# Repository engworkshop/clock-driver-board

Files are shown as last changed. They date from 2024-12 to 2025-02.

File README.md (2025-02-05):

# clock-driver-board
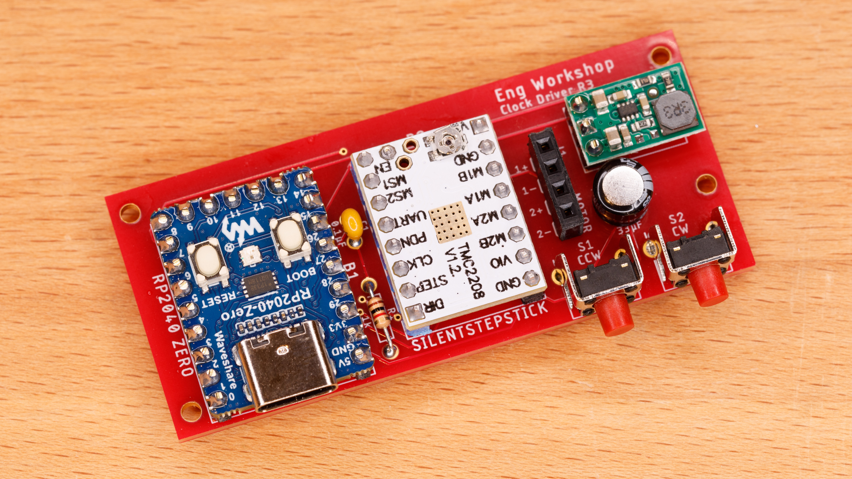
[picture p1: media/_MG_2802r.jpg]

This repository contains design files for an optional custom printed circuit board (PCB) for the [Mystery Clock](https://makerworld.com/en/models/764838) and [Hollow Clock 4 Remix](https://makerworld.com/en/models/875220) projects on [MakerWorld](https://makerworld.com/en/@EngWorkshop). This custom driver board incorporates 3 improvements. First, a dedicated real-time clock (RTC) chip, the Maxim DS3234, provides significantly greater timekeeping accuracy than the RP2040’s internal clock. The DS3234 incorporates temperature compensation to achieve its improved accuracy. Second, a dedicated stepper motor driver module provides quieter motor operation compared to the original design’s ULN2003 chip. The motor driver module incorporates the Trinamic TMC2208, which uses a “chopper drive” for quieter operation. Third, 2 pushbuttons allow fine adjustment of the hands.

The clock projects use a small, inexpensive 28BYJ-48 5V unipolar stepper motor. This motor must be converted to a bipolar configuration before it can be used with the clock driver board’s TMC2208 chip, which is designed for bipolar stepper motors. Motor conversion instructions are included at the bottom of this README file.

(All products shown or mentioned are items that I actually use and have found to work well. I have no relationship with any product supplier.)

## 1.&nbsp;&nbsp; The Circuit
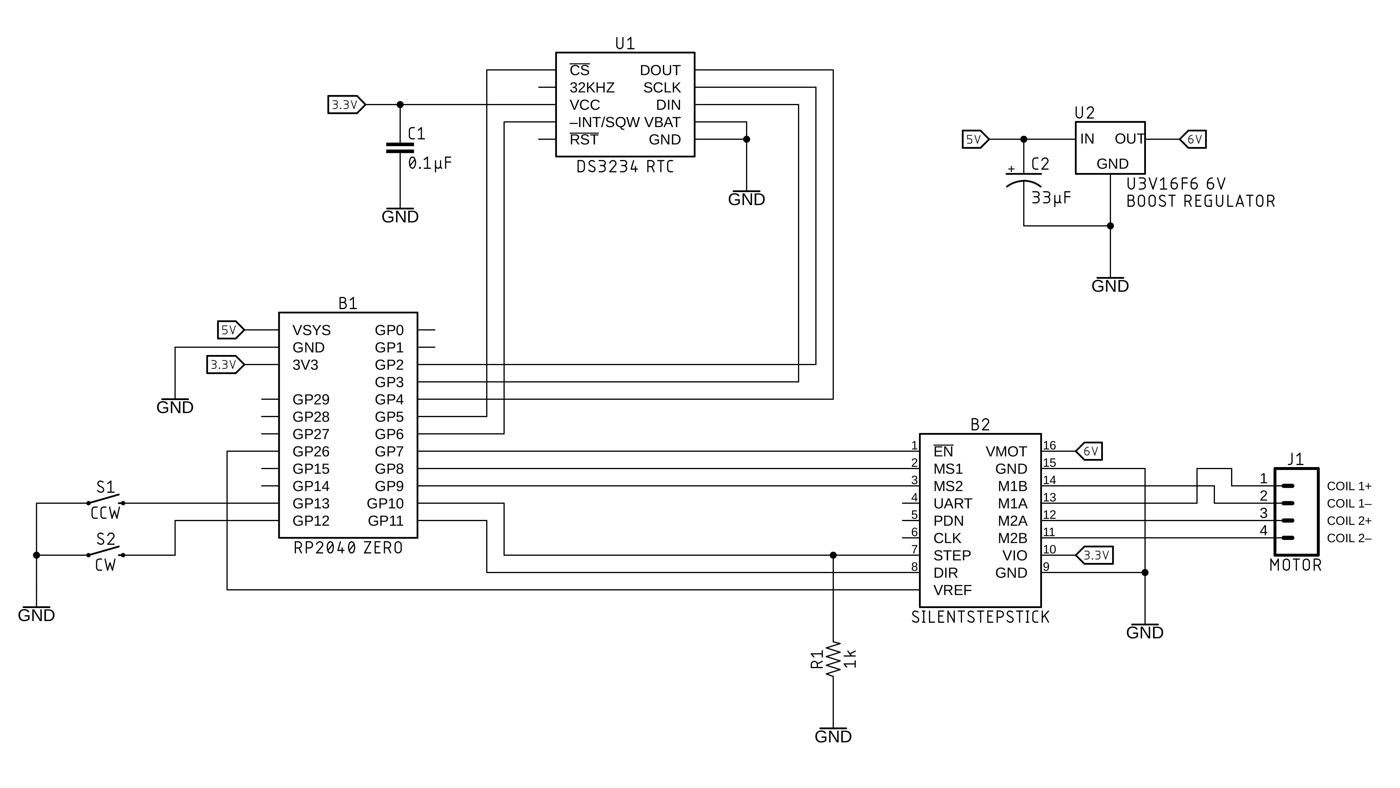
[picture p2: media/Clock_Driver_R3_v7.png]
schematic


**Circuit Description**

The RP2040 microcontroller communicates with the DS3234 RTC using the SPI bus. The clock chip is configured in software to send an interrupt to the microcontroller once every minute. In response to the interrupt, the microcontroller moves the minute hand through the TMC2208 motor driver. A pull-down resistor on the motor driver’s STEP input prevents spurious motor stepping during startup. A 6V boost regulator satisfies the motor driver module’s minimum supply voltage of 5.5V.

**Parts List**
- [Waveshare RP2040-Zero](https://www.waveshare.com/rp2040-zero.htm) microcontroller board without pin headers
- [TMC2208 SilentStepStick](https://www.amazon.com/gp/product/B08DFVZV5Q) stepper motor driver module
- [Pololu U3V16F6](https://www.pololu.com/product/4942) 6V boost voltage regulator
- Maxim DS3234 real-time clock chip ([DigiKey DS3234SN#-ND](https://www.digikey.com/en/products/detail/analog-devices-inc-maxim-integrated/DS3234SN/1197584))
- (2) C&K PTS645VK58-2LFS right angle tactile switches ([DigiKey CKN10965-ND](https://www.digikey.com/en/products/detail/c-k/PTS645VK58-2-LFS/3861398))
- 33 µF electrolytic capacitor (for example, [DigiKey P977-ND](https://www.digikey.com/en/products/detail/panasonic-electronic-components/ECE-A1EKS330/160557))
- 1 kΩ resistor (for example, [DigiKey 1.0KEBK-ND](https://www.digikey.com/en/products/detail/yageo/CFR-12JB-52-1K/4000))
- 0.1 µF ceramic capacitor (for example, [DigiKey 399-4264-ND](https://www.digikey.com/en/products/detail/kemet/C320C104K5R5TA/818040))
- male headers (for example, [DigiKey S1011EC-40-ND](https://www.digikey.com/en/products/detail/sullins-connector-solutions/PRPC040SAAN-RC/2775214))
- (4) M2 x 5 mm self-tapping pan head screws for mounting PCB (for example, [Amazon](https://www.amazon.com/gp/product/B07ZH9GJWP))
- [28BYJ-48 5V geared stepper motor](https://www.amazon.com/gp/product/B01CP18J4A)

## 2.&nbsp;&nbsp; Obtaining the PCB
The `board` folder contains the PCB’s Gerber files. In `upload to DKRed.zip`, I packaged the core files required by the [DKRed custom PCB](https://www.digikey.com/en/resources/dkred) service that I use. I included all Gerber files produced by Fusion 360, but I have only tested those required by DKRed:
- `copper_top.gbr` & `copper_bottom.gbr` — describes copper layers
- `soldermask_top.gbr` & `soldermask_bottom.gbr` — describes soldermask layers
- `silkscreen_top.gbr` & `silkscreen_bottom.gbr` — describes silkscreen layers
- `profile.gbr` - board outline
- `drill_1_16.xln` - drill locations

## 3.&nbsp;&nbsp; Soldering the PCB

### Step 3.1
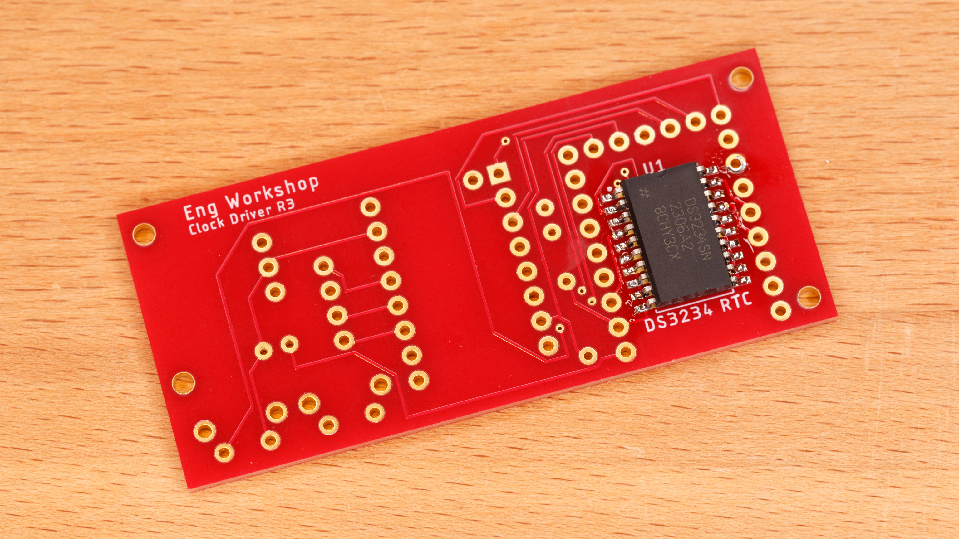
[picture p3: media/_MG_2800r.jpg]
solder clock chip

Solder the DS3234 clock chip on underside of the PCB. This is fairly easy to do with a fine-tipped soldering iron and desoldering braid (see SparkFun’s [tutorial on soldering SMD devices](https://www.sparkfun.com/tutorials/36)). No dedicated SMD soldering equipment is necessary.

### Step 3.2
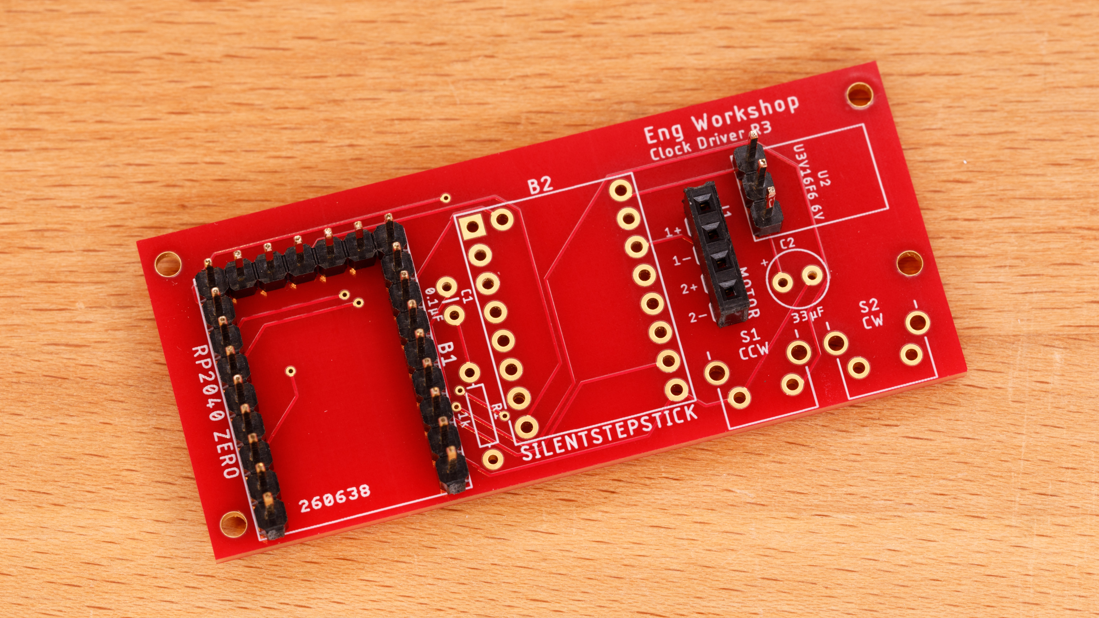
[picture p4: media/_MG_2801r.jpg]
solder headers

Solder male headers for the RP2040 Zero and voltage regulator. Optional: solder a female header for the motor. If you are making a Mystery Clock or Hollow Clock 4 Remix, **DO NOT SOLDER** a connector for the motor. Instead, the motor wires will need to be soldered directly to the PCB in order to fit in the clock base.

### Step 3.3
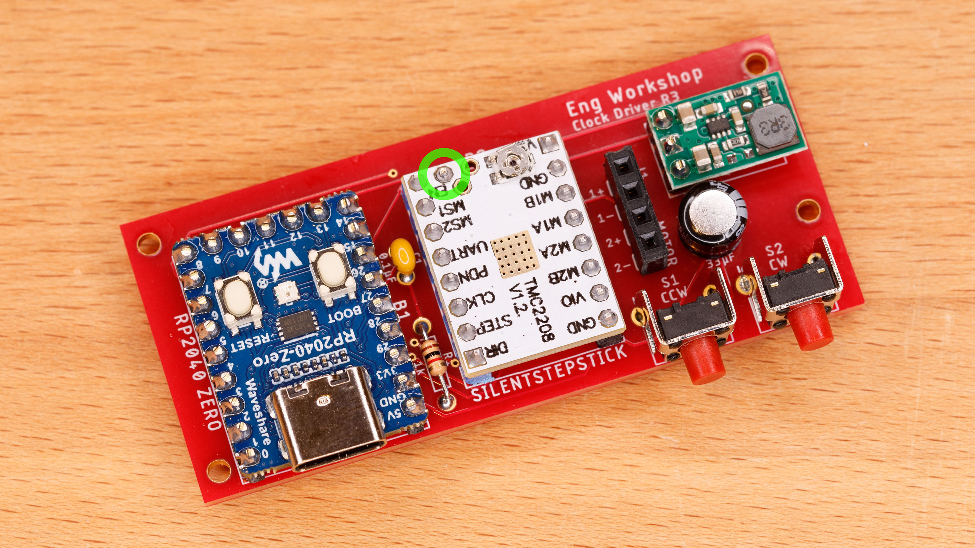
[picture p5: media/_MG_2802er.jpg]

Solder the remaining parts onto the PCB. Note that an extra header pin (circle) must be soldered to the SilentStepStick. Trim all header pins protruding on top or bottom of the PCB so they are flush with their respective solder connections. The PCB can be mounted with M2 screws.

## 4.&nbsp;&nbsp; Converting the Stepper Motor from Unipolar to Bipolar

### Step 4.1
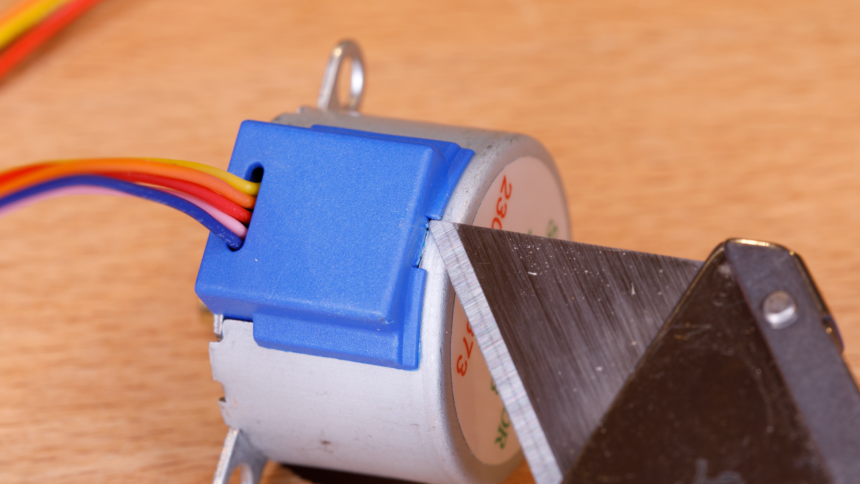
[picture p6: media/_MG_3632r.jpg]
remove motor cover

With a utility knife, score the small tab on the plastic motor cover until it breaks off. Pry open the cover.

### Step 4.2
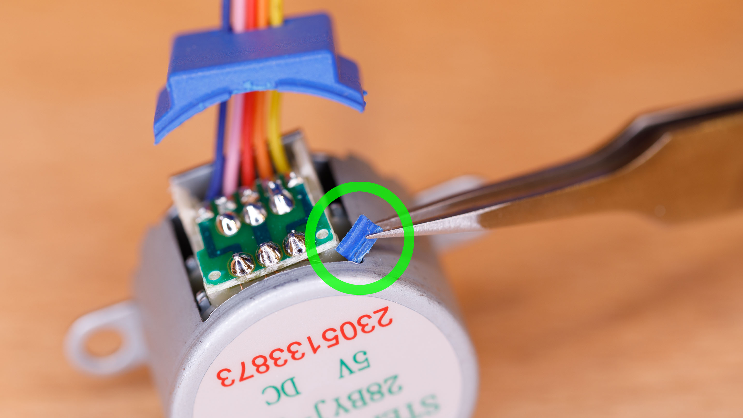
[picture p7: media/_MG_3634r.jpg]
remove plastic tab

Remove the small plastic tab that was broken off in Step 3.1. Be careful not to damage the extremely delicate motor windings.

### Step 4.3
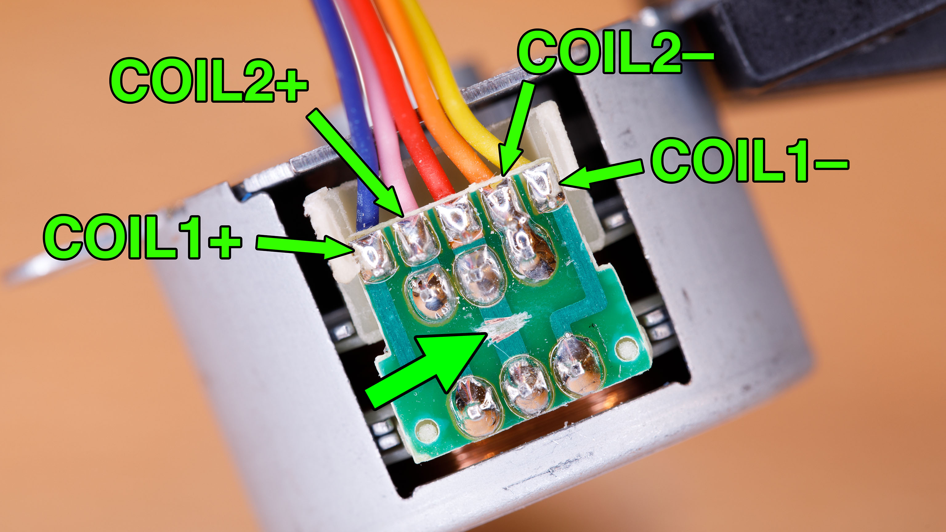
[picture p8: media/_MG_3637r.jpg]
cut PCB trace

With a utility knife, carefully cut/scrape the center PCB trace (large arrow). (See SparkFun’s [tutorial on cutting PCB traces](https://learn.sparkfun.com/tutorials/how-to-work-with-jumper-pads-and-pcb-traces/cutting-a-trace-between-jumper-pads).) The middle (red) wire is no longer functional and may be clipped off. Take note of the wire color corresponding to each coil connection.

### Step 4.4
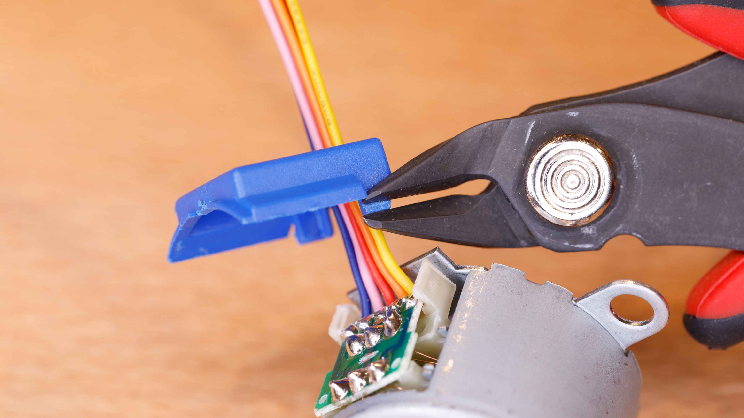
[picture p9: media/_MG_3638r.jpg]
trim cover tabs

Glue the plastic cover back on the motor. If necessary, trim the remaining tabs so that the cover can be inserted easily.

## 5.&nbsp;&nbsp; The Code

The `code` folder contains a single Arduino code file, `mystery-clock-tmc.ino`. The code’s comment block details its dependencies and operation. The following are required to install the code:

- [Arduino IDE](https://www.arduino.cc/en/software), if you do not already have it
- Earle Philhower’s [Raspberry Pi Pico RP2040 processor Arduino core](https://arduino-pico.readthedocs.io/en/latest/) using the Arduino Boards Manager
- SparkFun’s [DS3234 RTC library](https://github.com/sparkfun/SparkFun_DS3234_RTC_Arduino_Library) for Arduino

## 6.&nbsp;&nbsp; Operating Instructions

The pushbuttons move the clock hands clockwise or counterclockwise. Pushing a button momentarily causes the minute hand to move one minute. Pressing and holding a button moves the minute hand continuously.

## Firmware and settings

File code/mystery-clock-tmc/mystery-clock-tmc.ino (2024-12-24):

/*
	mystery-clock-tmc.ino:  TMC2208 Motor Driver for Mystery Clock

	Copyright 2024 by John Eng

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
	This program is distributed in the hope that it will be useful, but
	WITHOUT ANY WARRANTY; without even the implied warranty of MERCHANTABILITY
	or FITNESS FOR A PARTICULAR PURPOSE.  For more details, see
	https://www.gnu.org/licenses/gpl-3.0.en.html
	--------------------

	REVISION HISTORY:
	Oct 2024   Initial version, based on hollow-clock.ino

	HARDWARE COMPONENTS:
	Waveshare RP2040 Zero - similar to Raspberry Pi Pico
	Maxim DS3234 realtime clock
	Watterott SilentStepStick clone, based on Trinamic TMC2208
	Elegoo 28BYJ-48 stepper motor, modified for bipolar operation
		32 steps per revolution of ungeared motor
		9:32, 11:22, 9:27, 8:24 = exact 1:64 gear reduction
		therefore, 2048 steps per revolution
		verified by disassembly of gearbox and inspection of gears
	Gearing based on Hollow Clock 4 design by Shiura
		https://www.thingiverse.com/thing:5636482
		1 rotation of motor shaft turns minute gear 12 steps
		minute gear has 90 teeth
		therefore, motor must turn 90/12 = 7.5 rotations per hour
			or 90/12/60 = 1/8 rotation per minute
			or (1/8)*2048 = 256 steps per minute

	SOFTWARE REQUIREMENTS:  Arduino IDE with Earle Philhower's Arduino core
	for the Raspberry Pi Pico RP2040 processor installed, which is documented
	at

		https://github.com/earlephilhower/arduino-pico
		https://arduino-pico.readthedocs.io/en/latest

	Be sure to check and select correct serial port whenever connecting
	controller to computer, even if correct board identity is shown.

	SparkFun DS3234 RTC Arduino library installed.  The SparkFun library is
	old and must be installed from .zip file (Arduino > Sketch < Include
	Library > Add .ZIP Library).  The SparkFun library can be found at

		https://github.com/sparkfun/SparkFun_DS3234_RTC_Arduino_Library.

	PROGRAMMING NOTES
	1.	Arduino has a stepper motor library, but you cannot turn motor power
		on/off.  So, this code implements its own stepper motor functions.
		Otherwise, the motor gets pretty hot under normal conditions.
	2.	The SparkFun RTC library has some convenient features, but it is too
		simplistic for serious use.  It does not provide an explicit method
		for enabling only one of the RTC interrupts, nor does it provide a
		function for clearing the alarm/interrupt flag explicitly.  These
		deficiencies result in undesirable behavior when trying to use
		interrupts.  I had to add functions to provide more explicit control,
		essentially hijacking the SPI bus from the SparkFun library, meaning
		that I call SPI library functions without explicitly initializing SPI
		by calling SPI.begin().  SPI.begin() is called within the SparkFun RTC
		library.
	3.	Earle Philhower's Arduino core includes additional SPI functions that
		allow the SPI pins to be specified explicitly before SPI.begin() is
		called by third party libraries.  Smart!
	4.	When using Arduino hardware, disabling interrupts with noInterrupts()
		also disables motor stepping because motor stepping relies on delay(),
		and delay() requires interrupts to be enabled.  I assumed this is also
		true of the RP2040, but I didn't test it.

	OPERATION:  Press and hold the CW or CCW button to move the hands.  Press
	release to move the minute hand by one minute.  The clock's minute counter
	is synchronized to the last button press.

	If a button is pressed during startup, the TMC2208's reference voltage and
	corresponding motor current will be shown in the Arduino console.  The
	motor requires about a 220 mA current.  The reference voltage, and thus the
	motor current, are controlled by a small potentiometer on the
	SilentStepStick.  Press a button again to stop the console output and
	resume normal operation.

	To do:
	implement 2-speed motor switching
*/

///////////////////////////////////////////////////////////////////////////////
//
//   LIBRARIES, CONSTANTS, AND VARIABLES
//
///////////////////////////////////////////////////////////////////////////////

// Library headers
#include <SPI.h>
#include <SparkFunDS3234RTC.h>

// Constants for controller board pins
const int ENABLE_PIN   = 7;   // Motor driver: enable, active LOW
const int MSELECT1_PIN = 8;   // Motor driver: microstep configuration
const int MSELECT2_PIN = 9;   // Motor driver: microstep configuration
const int STEP_PIN     = 10;  // Motor driver: step motor, active on rising edge
const int DIR_PIN      = 11;  // Motor driver: motor direction
const int SCK_PIN      = 2;   // RTC: serial clock
const int PICO_PIN     = 3;   // RTC: peripheral in, controller out
const int POCI_PIN     = 4;   // RTC: peripheral out, controller in
const int RTC_CS_PIN   = 5;   // RTC: chip select (-CS)
const int RTC_INT_PIN  = 6;   // RTC: interrupt output(-INT/SQW)
const int CW_BTN_PIN   = 12;  // Button for moving hands counterclockwise; connected to GND
const int CCW_BTN_PIN  = 13;  // Button for moving hands clockwise; connected to GND
const int VREF_PIN     = 26;  // Motor driver: reference voltage

// Timing constants
const unsigned long POWER_DELAY     = 300;   // Wait for power up or down (ms)
const unsigned long DEBOUNCE_DELAY  = 10;    // Button debounce delay (ms)

// Motor constants
const int STEPS_PER_REVOLUTION = 32*64;               // Number of motor steps to turn geared shaft one revolution
const int STEPS_PER_MINUTE = STEPS_PER_REVOLUTION/8;  // Number of motor steps to move minute hand 1 minute
const int DIR_FORWARD = HIGH;                         // Determines which DIR_PIN level is considered "forward"
const int DIR_BACKWARD = LOW;                         // Determines which DIR_PIN level is considered "backward"

// Constants and variables for button state tracking
const int N_BUTTONS = 2;  // Number of connected button pins
int gBtnPin[] = {         // Table of button pin numbers, corresponding to gLastBtnState[] and gLastBtnTimestamp[]
	CW_BTN_PIN,
	CCW_BTN_PIN
	};
int gLastBtnState[N_BUTTONS];                // Last known state (LOW or HIGH) of button, maintained by readButtonByIndex()
unsigned long gLastBtnTimestamp[N_BUTTONS];  // Last time button was noted to change state
const int BUTTON_NONE  = -1;                 // "Null" button "pin" returned by button subroutines

// Constants and variables for reading of TMC2208 reference voltage
const int ADC_BUFFER_SIZE = 200;    // Size of circular buffer for storing ADC readings
int gAdcReadings[ADC_BUFFER_SIZE];  // Circular buffer for storing ADC readings
int gReadingsPtr = 0;               // Pointer to position of next ADC reading in circular buffer
long gReadingsSum = 0;              // Summation of ADC readings for averaging


// Table for microstep configuration
int gMicrostepConfig[][4] = {
	{8,  LOW,  LOW,  2000},  // microsteps, MSELECT1, MSELECT2, motor step time
	{2,  HIGH, LOW,  3000},
	{4,  LOW,  HIGH, 3000},
	{16, HIGH, HIGH, 2000}
	};

// Global variables
int gMicrosteps;                          // Number of microsteps per full step, initialized in setup()
unsigned int gMotorStepDelay;             // Delay between microsteps (microseconds), initialized in setup()
int gMotorDirection;                      // Current motor direction, initialized in setup()
int gNextAlarm = 59;                    // Second of the minute to generate alarm interrupt
volatile boolean gMoveMotorFlag = false;  // Set by interrupt service routine to signal need to move motor

///////////////////////////////////////////////////////////////////////////////
//
//   STANDARD ARDUINO IDE METHODS
//
///////////////////////////////////////////////////////////////////////////////

// Arduino initialization
void setup() {
	// Configure signal pins
	pinMode(ENABLE_PIN,   OUTPUT);
	pinMode(MSELECT1_PIN, OUTPUT);
	pinMode(MSELECT2_PIN, OUTPUT);
	pinMode(STEP_PIN,     OUTPUT);
	pinMode(DIR_PIN,      OUTPUT);
	pinMode(RTC_CS_PIN,   OUTPUT);
	pinMode(RTC_INT_PIN,  INPUT_PULLUP);
	pinMode(CW_BTN_PIN,   INPUT_PULLUP);
	pinMode(CCW_BTN_PIN,  INPUT_PULLUP);
	// Initialize digital outputs
	digitalWrite(ENABLE_PIN,   HIGH);
	digitalWrite(STEP_PIN,     LOW);
	digitalWrite(DIR_PIN,      DIR_FORWARD);
	digitalWrite(RTC_CS_PIN,   HIGH);
	gMotorDirection = DIR_FORWARD;
	setMicrosteps(8);  // Initialize gMicrosteps, gMotorStepDelay, MSELECT1_PIN, and MSELECT2_PIN
	// Initialize button state arrays
	for (int i = 0; i < N_BUTTONS; i++) {
		gLastBtnState[i] = HIGH;
		gLastBtnTimestamp[i] = millis();
		}
	delay(DEBOUNCE_DELAY*2);  // Debounce delay required before immediate first use!
	// If a button is pressed at startup, show TMC2208 reference voltage on console
	if (readButtons() != BUTTON_NONE) {
		showRefVoltage();  // Returns after a button is pressed again
		}
	// Initialize motor position
	motorPower(true);
	motorPower(false);
	// Initialize RTC chip
	rtc.begin(RTC_CS_PIN);      // Initialize SparkFun RTC library
	initTime();                 // Set RTC to a dummy time and date
	rtc.setAlarm1(gNextAlarm);  // Set alarm for specific second of a minute
	configureInterrupts();      // Configure RTC chip for interrupt generation
	// Set up interrupt service routine
	attachInterrupt(digitalPinToInterrupt(RTC_INT_PIN), handleInterrupt, FALLING);
	}

// Arduino main execution loop
void loop() {
	// Check if motor needs to be moved
	if (gMoveMotorFlag) {  // Flag set in handleInterrupt()
		motorPower(true);
		motorStep(STEPS_PER_MINUTE);
		motorPower(false);
		gMoveMotorFlag = false;
		}
	// Handle button presses
	checkButtons();
	}

///////////////////////////////////////////////////////////////////////////////
//
//   MAIN SUBROUTINES
//
///////////////////////////////////////////////////////////////////////////////

// Manually move motor with CW and CCW buttons
void checkButtons() {
	switch (readButtons()) {
		case CW_BTN_PIN:
			handleButton(CW_BTN_PIN);
			break;
		case CCW_BTN_PIN:
			handleButton(CCW_BTN_PIN);
			break;
		}
	}

// Handle button press and release
void handleButton(int btnPin) {
	// Turn on motor
	motorPower(true, false);
	// Move motor continuously if button held down
	unsigned long t0 = millis();
	while (readButton(btnPin) == LOW) {
		if (millisSince(t0) >= POWER_DELAY) {
			motorStepOne((btnPin == CW_BTN_PIN) ? 1 : -1);
			delayMicroseconds(gMotorStepDelay);
			}
		}
	// Move motor one minute if button pressed and released
	unsigned long t1 = millisSince(t0);
	if (t1 < POWER_DELAY) {
		delay(POWER_DELAY - t1);
		motorStep((btnPin == CW_BTN_PIN) ? STEPS_PER_MINUTE : -STEPS_PER_MINUTE);
		}
	// Reset time register
	initTime();
	// Turn off motor
	motorPower(false);
	}

// Interrupt service routine
void handleInterrupt() {
	clearAlarmFlags();
	gMoveMotorFlag = true;  // Indicate that motor needs to be moved
	}

///////////////////////////////////////////////////////////////////////////////
//
//   SUBROUTINES FOR READING TMC2208 REFERENCE VOLTAGE
//
///////////////////////////////////////////////////////////////////////////////

// Show TMC2208 reference voltage on console
void showRefVoltage() {
	// Initialize serial port
	Serial.begin();  // USB port requires no baud rate
	while (!Serial) {}
	// Initialize buffer of ADC readings
	for (int i = 0; i < ADC_BUFFER_SIZE; i++) {
		delay(2);
		gAdcReadings[i] = analogRead(VREF_PIN);
		gReadingsSum += long(gAdcReadings[i]);
		}
	// Wait until button released
	while (readButtons() != BUTTON_NONE) {}
	// Voltage polling loop
	do {
		int vref = updateMillivolts(VREF_PIN);
		float motorCurrent = (325.0*float(vref))/(140.0*sqrt(2.0)*2500.0);  // Formula from TMC2208 data sheet
		motorCurrent *= 1000.0;
		Serial.print(vref);
		Serial.print(" mV   ");
		Serial.print(int(motorCurrent + 0.5));
		Serial.println(" mA");
		}
	while (readButtons() == BUTTON_NONE);
	while (readButtons() != BUTTON_NONE) {}
	}

// Read one ADC value, update running average of voltage
int updateMillivolts(int adcPin) {
	// Subtract old reading from summation
	gReadingsSum -= long(gAdcReadings[gReadingsPtr]);
	// Store new reading
	delay(2);
	gAdcReadings[gReadingsPtr] = analogRead(adcPin);
	// Add new reading to summation
	gReadingsSum += gAdcReadings[gReadingsPtr];
	// Update circular buffer pointer
	gReadingsPtr++;
	if (gReadingsPtr >= ADC_BUFFER_SIZE) gReadingsPtr = 0;
	// Calculate voltage in millivolts
	float v = float(gReadingsSum)/float(ADC_BUFFER_SIZE);
	v = 3300.0*v/1024.0;
	return (int(v + 0.5));
	}

///////////////////////////////////////////////////////////////////////////////
//
//   RTC SUBROUTINES
//
///////////////////////////////////////////////////////////////////////////////

// Set RTC to a dummy time
void initTime() {
	rtc.setTime(0, 0, 0, 7, 25, 11, 23);  // Set to midnight of Saturday, November 25, 2023
	clearAlarmFlags();
	gMoveMotorFlag = false;  // In case interrupt occurred prior to calling this method
	}

// Enable alarm 1 and disable alarm 2 interrupts
void configureInterrupts() {
	byte registerValue = readRtc(0x0E);
	writeRtc(0x8E, (registerValue & (~0x02)) | 0x01);
	}

// Clear both RTC alarm flags
void clearAlarmFlags() {
	byte registerValue = readRtc(0x0F);
	writeRtc(0x8F, registerValue & (~0x03));
	}

// Read value from RTC register
byte readRtc(byte address) {
	digitalWrite(RTC_CS_PIN, LOW);
	SPI.transfer(address);
	byte r = SPI.transfer(0x00);
	digitalWrite(RTC_CS_PIN, HIGH);
	return (r);
	}

// Write value to RTC register
void writeRtc(byte address, byte value) {
	digitalWrite(RTC_CS_PIN, LOW);
	SPI.transfer(address);
	SPI.transfer(value);
	digitalWrite(RTC_CS_PIN, HIGH);
	}

///////////////////////////////////////////////////////////////////////////////
//
//   MOTOR SUBROUTINES
//
///////////////////////////////////////////////////////////////////////////////

// Set number of microsteps
void setMicrosteps(int microsteps) {
	// Determine size of configuration array
	int len = sizeof(gMicrostepConfig)/sizeof(gMicrostepConfig[0]);
	// Scan configuration array for matching number of microsteps
	for (int i = 0; i < len; i++) {
		if (microsteps == gMicrostepConfig[i][0]) {
			gMicrosteps = microsteps;
			digitalWrite(MSELECT1_PIN, gMicrostepConfig[i][1]);
			digitalWrite(MSELECT2_PIN, gMicrostepConfig[i][2]);
			gMotorStepDelay = gMicrostepConfig[i][3];
			return;
			}
		}
	// Do nothing if specified microsteps is invalid
	}

// Move motor given number of steps
void motorStep(long n) {
	if (n == 0) return;
	long nAbs = abs(n);
	for (long i = 0; i < nAbs; i++) {
		motorStepOne(n);
		delayMicroseconds(gMotorStepDelay);
		}
	}

// Move motor one step in given direction
void motorStepOne(long direction) {
	// Set motor direction
	motorDirection(direction);
	// Step motor the number of microsteps equivalent to a full step
	for (int i = 0; i < gMicrosteps; i++) {
		digitalWrite(STEP_PIN, HIGH);
		digitalWrite(STEP_PIN, LOW);  // Pulse width measured to be 600 ns with Waveshare RP2040 Zero
		delayMicroseconds(gMotorStepDelay);
		}
	}

// Turn motor coils on/off with delay to let things settle down
void motorPower(boolean turnOn) {
	motorPower(turnOn, true);
	}

// Turn motor power on/off using ENABLE pin
void motorPower(boolean turnOn, boolean delayFlag) {
	if (turnOn) {
		digitalWrite(ENABLE_PIN, LOW);
		if (delayFlag) delay(POWER_DELAY);
		}
	else {
		if (delayFlag) delay(POWER_DELAY);
		digitalWrite(ENABLE_PIN, HIGH);
		}
	}

// Set motor direction while preventing redundant calls to digitalWrite()
void motorDirection(long direction) {
	if (direction >= 0) {
		if (gMotorDirection != DIR_FORWARD) {
			digitalWrite(DIR_PIN, DIR_FORWARD);
			gMotorDirection = DIR_FORWARD;
			}
		}
	else {
		if (gMotorDirection != DIR_BACKWARD) {
			digitalWrite(DIR_PIN, DIR_BACKWARD);
			gMotorDirection = DIR_BACKWARD;
			}
		}
	}

///////////////////////////////////////////////////////////////////////////////
//
//   BUTTON SUBROUTINES
//
///////////////////////////////////////////////////////////////////////////////

// Read state of all button switches, return identifier of button pressed
int readButtons() {
	for (int i = 0; i < N_BUTTONS; i++) {
		if (readButtonByIndex(i) == LOW) return (gBtnPin[i]);
		}
	return (BUTTON_NONE);
	}

// Read state of one button switch given button pin number (active LOW)
int readButton(int btnPin) {
	int btnIndex = pinToIndex(btnPin);
	return (readButtonByIndex(btnIndex));
	}

// Read state of one button switch with debouncing (active LOW), given index to button arrays
int readButtonByIndex(int btnIndex) {
	// Don't read button during debounce period
	if (millisSince(gLastBtnTimestamp[btnIndex]) < DEBOUNCE_DELAY) {
		return (gLastBtnState[btnIndex]);
		}
	// Read current button state
	int newBtnState = digitalRead(gBtnPin[btnIndex]);
	// If button state has changed, save new state along with a timestamp
	if (newBtnState != gLastBtnState[btnIndex]) {
		gLastBtnState[btnIndex] = newBtnState;
		gLastBtnTimestamp[btnIndex] = millis();
		}
	// Return LOW if button pressed, HIGH if not pressed
	return (newBtnState);
	}

// Convert button pin number to array index
int pinToIndex(int btnPin) {
	for (int i = 0; i < N_BUTTONS; i++) {
		if (btnPin == gBtnPin[i]) return (i);
		}
	return (0);  // Default to 0 for safety to avoid out-of-bounds index
	}

///////////////////////////////////////////////////////////////////////////////
//
//   UTILITY SUBROUTINES
//
///////////////////////////////////////////////////////////////////////////////

// Calculate milliseconds since last activity (modified from adb-blue-kbd.ino)
// Correct even when timer rolls over as long as all arithmetic is unsigned
unsigned long millisSince(unsigned long baseTime) {
	unsigned long d = millis() - baseTime;
	return (d);
	}

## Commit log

2024-12-17 Create Clock Driver R3 v7.png
2024-12-17 Rename schematic
2024-12-24 Upload board files
    [copper_bottom.gbr, copper_top.gbr, drill_1_16.xln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]

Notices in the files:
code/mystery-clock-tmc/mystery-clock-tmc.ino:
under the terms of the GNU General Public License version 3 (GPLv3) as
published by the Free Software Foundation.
